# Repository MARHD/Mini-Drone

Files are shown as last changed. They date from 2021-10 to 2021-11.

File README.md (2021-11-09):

# Mini-Drone
Design of a Mini Drone for University of Cape Town EEE4022S final year project.

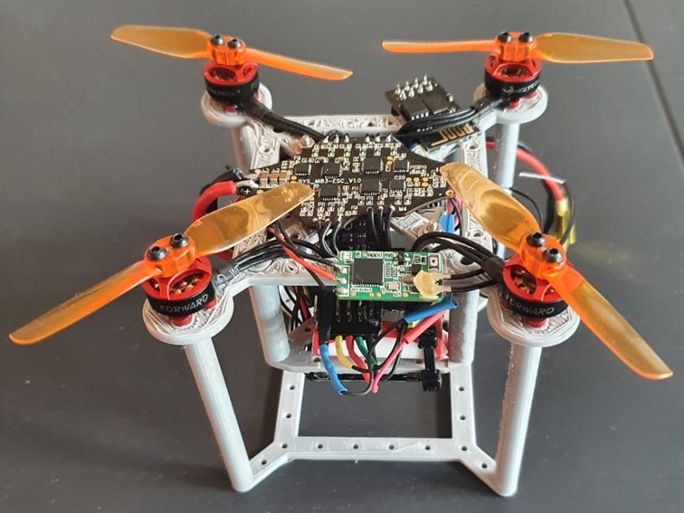
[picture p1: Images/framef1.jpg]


Original project description:
Ardupilot is a professional grade open-source autopilot software stack. This
project requires a student to design a mini-drone (<250g) running the Ardupilot
firmware. An example of analogous drones are linked below. In addition to
designing and building this drone the student must integrate an openflow sensor,
used to facilitate drones holding position by using input from a downwards facing
camera.

Original Deliverables:
1. A literature review briefly summarising drone autopilot software, currently
available mini-drones, recent work using openflow sensors for localisation
2. A functioning mini-drone
3. All design files for (2) including mechanical, electrical, and software build
instructions in a documented public git repository
4. A qualification of the performance of the resulting design
5. The final thesis report, poster, and presentation

## Specifications
- Quadracopter with optical flow sensor and range finder
- Cost: R 5273 (Excluding optical flow sensor, wires, shipping, compatible transmitter and 2S LiPo battery charger), price can be reduced with the replacement of the Pixracer for an Omnibus F4 Pro
- Uses Pixracer R15 flight controller/autopilot, running ArduPilot
- Take-off weight including battery: 107g
- Recommended payload capacity: 60g
- Flight Time with no additional payload: 7-8min hover
- Assembly and test flight time: 2-3hrs (once experienced)

## Getting started
Note: Some assembly tools as well as a means of 3D printing (PLA) are required for assembly.  All 3D printable models are available in [Mechanical Design](./Mechanical%20Design) as Fusion 360 design files, as well as stl files

All required components and suppliers are listed in the following [BOM](./Instructions/BOM.xlsx)

Build instructions are available [here](./Instructions/README.md)

Read through the written report to learn how the components were chosen. Available [here](./report.pdf)

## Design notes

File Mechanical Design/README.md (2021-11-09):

# Design Files

## Final design used. Files to print, [here](./STL%20Files) and file to edit, [here](./Fusion%20Files/Frame%20Final.f3z)



## Older designs
### First design (incomplete). File to edit, [here](./Fusion%20Files/Final%201.f3z)

### Second design (not recommended). File to edit, [here](./Fusion%20Files/Final%202.f3z)

### Third design (works but flimsy upon crash). File to edit, [here](./Fusion%20Files/Final%203.f3z)


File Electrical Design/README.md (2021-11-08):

# Electrical Design

The schematics for the Pixracer flight controller, the microcontroller used on the Pixracer, 
the Flowdeck V2, the Flow Breakout, the Bitcraze Crazyflie 2.1 and the datasheets for,
the PMW3901 (optical flow sensor) and VL53L1X (range finder), are all available here.

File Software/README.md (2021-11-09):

# Software

The compiled .apj file for the project can be found [here](/ArduCopter-4.1%20Custom/Builds/). 
It enables SPI on the port originally designed for the ESP-01 module, and is setup for a pixart 
optical flow sensor (PMW3901)

The ArduCopter parameters used, can be found [here](/ArduCopter-4.%20Custom/Mission%20planner%20Parameters/).
You will still need to calibrate your sensors and some options may need you to follow the ArduCopter guides (such as tuning).

The files which were modified in the firmware can be found [here](/ArduCopter-4.1%20Custom/Modified%20files/).
The unmodified file is also available for comparison.

Finally the Source code for the build of ArduCopter used is available [here](/ArduCopter-4.1%20Custom/Source/)

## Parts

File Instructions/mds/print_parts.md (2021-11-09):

# Printing & assembling plastic parts

1. Print the two .stl files, [here](/./Mechanical%20Design/STL%20Files/Frame_top.stl) for the top frame and [here](/./Mechanical%20Design/STL%20Files/Frame_carriage.stl) for the carriage. Optionally the Stand [here](/./Mechanical%20Design/STL%20Files/Stand.stl) can also be printed.



2. Use a hobby knife to remove the 3D printed supports from these locations. 

 

3. Rotate the carriage such that the foreward arrow is facing foreward, and the posts are facing upwards. 



4. Then rotate the top frame such that the foreward arrow is also facing foreward, and the posts are facing downwards. 



5. Use either a hobby knife or a de-burring tool to clean up any imperfections on the large post holes, the large motor holes on the upper frame and the posts of the carriage. 



6. Apply some super glue into each of the large post holes on the top frame.

  

7. Fit the two parts together with the large holes of the top frame on the carriage posts, such that the top of the posts are flush with the top carriage, as seen in the previous image. 
 
8. Let the glue dry...  

9. Move onto [Mounting the Pixracer](./mount_pixracer.md)

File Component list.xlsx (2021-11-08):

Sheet: Sheet1
Component | Amount | Ind Price | Price | Total | Weight (g) | Link
Motor | 4 | 0 | 0 | 1161.06 | 21.2 | https://hobbyking.com/en_us/brushed-motor-4-pcs-per-set.html?queryID=001191b567772c1bde66302cd4100a57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
Frame | 1 | 0 | 0 |  |  | https://www.rcworld.co.za/product_details.php?proid=298
Mosfets | 4 | 2.3 | 9.2 |  |  | https://flyingrobot.co/collections/speed-controllers/products/flycolor-raptor-bls-pro-blheli_s-30a-2-4s-dshot-brushless-esc
Flight Controller | 1 | 422.5 | 422.5 |  |  | https://www.rcworld.co.za/product_details.php?proid=1357
Battery | 1 | 288.36 | 288.36 |  |  | https://www.rcworld.co.za/product_details.php?proid=308
Receiver | 1 | 280 | 280 |  |  | https://www.goblinhobbies.co.za/fpv/receiver/frsky-xm-sbus-mini-receiver.html
Camera | 1 | 0 | 0 |  | 1.6 | https://store.bitcraze.io/collections/decks/products/flow-deck-v2
 |  |  |  |  |  |  |  |  |  | Choices based on stock availability
for ardupilot
168Mhz and 1MB is minimum on mC
100mm 1s drone | weight | maybe
motors |  | 11 |  | https://micro-motor-warehouse.com/collections/all-motors/products/cl-0716-17 | . |  |  |  |  |  |  | FC requirements
frame | 28 | 10 | 11 | https://www.rcworld.co.za/product_details.php?proid=292 | https://flyingrobot.co/collections/frames-1/products/beta95x-v3-frame-kit | https://www.rcworld.co.za/product_details.php?proid=298 | . |  |  |  |  | Support ardupilot
fc | 5 | 11 | 7 | https://www.rcworld.co.za/product_details.php?proid=1357 | . |  |  |  |  |  |  | 168Mhz and 1MB
receiver | 3 | 1 |  | https://www.rcworld.co.za/product_details.php?proid=1384 | . |  |  |  |  |  |  | aka STM32F4
camera | 2 | 1.6 |  |  | . |  |  |  |  |  |  | 1S battery
battery | 0 | 14 |  | https://www.rcworld.co.za/product_details.php?proid=198 | . |  |  |  |  |  |  | SPI and I2C because flowdeck needs both
props | 5 | 56 | 13 | https://flyingrobot.co/collections/3inch-propellers/products/hq-durable-prop-t65mm-5cw-5ccw-poly-carbonate | . |  |  |  |  |  |  | cheap
wires+misc | 5
total | 48
150mm drone | weight | maybe
motors |  | 20 |  | https://micro-motor-warehouse.com/products/cl-0820-15 | .
frame | 40 | 35 |  | https://www.rcworld.co.za/product_details.php?proid=1174 | . | https://flyingrobot.co/collections/frames-1/products/tbs-source-podracer-5 | .
fc | 5 |  |  |  | .
receiver | 3 |  |  |  | .
camera | 2 |  |  |  | .
battery | 0 |  |  |  | .
props | 10 | 8 |  | https://flyingrobot.co/collections/4inch-propellers/products/hqprop-t4x2x3-2cw-2ccw-poly-carbonate-grey | .
wires+misc | 10
total | 70
200mm drone | weight | maybe
motors |  | 6.1*4 |  |  | .
frame | 47 | 59 |  | https://www.rcworld.co.za/product_details.php?proid=1356 | . | https://flyingrobot.co/collections/frames-1/products/tbs-source-podracer-5 | .
fc | 5 |  |  |  | .
receiver | 3 |  |  |  | .
camera | 2 |  |  |  | .
battery | 0 |  |  |  | .
props | 15 | 14.8 |  | https://flyingrobot.co/collections/6inch-propellers/products/ethix-k2-bubble-gum-2cw-2ccw-poly-carbonate | .
esc |  | 7x4 |  | https://www.rcworld.co.za/product_details.php?proid=1233 | .
wires+misc | 20
total | 92
Quad or Hexa
El cheapo hex | weight | maybe |  | main |  | alt
motors | 17.5 | 30 or 17.5 | 5 or 2.9 |  | .
frame | 32 | 50 | 62 | https://www.banggood.com/Flywoo-Firefly-Hex-Nano-90mm-GOKU-F4-13A-ESC-4S-1_6-Inch-Hexacopter-Micro-FPV-Racing-Drone-BNF-NO-GPS-Version-w-or-5_8G-450mW-VTX-Cad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 | . | https://www.banggood.com/Flywoo-HEXplorer-LR-4-Hexa-copter-HD-or-Analog-Version-3mm-Arm-Thickness-Carbon-Fiber-Frame-Kit-for-FPV-Racing-RC-Drone-p-1805738.htm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 | .
fc | 8 | 11 |  | https://www.banggood.com/Omnibus-F4SD-32K-Betaflight_3_2_0-STM32-F405-Flight-Controller-OSD-5V-3A-BEC-30_5X30_5mm-p-1211677.html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 | https://www.goblinhobbies.co.za/fpv/controller/xrotor-flight-controller-f4-g3-w-osd-for-fpv-racing.html | http://replacementparts-skyrockettoys-com.3dcartstores.com/2018-Fury-Flight-Board-motor-combo_p_158.html | .
receiver | 3 | 10 |  | https://www.rcworld.co.za/product_details.php?proid=1384 | . | https://flyingrobot.co/collections/rx/products/frsky-xm-receiver | . |  |  |  | component choice table
camera | 2 | 1.6 |  |  | . |  |  |  |  |  | add all trials and tribulations into report
battery |  | 15 |  | 450mah 35/50c | .
props | 6 | 10 |  | https://flyingrobot.co/collections/3inch-propellers/products/hq-durable-prop-t65mm-5cw-5ccw-poly-carbonate | .
esc\mosfet board | 2 | 2 |  | https://www.flyingtech.co.uk/electronics/brushed-mosfet-motor-driver-board-pdb-micro-drone | . |  |  | arduino nano 8g
Arduino + transceiver | 11 | 8+3 |  | https://www.robotics.org.za/ESP-01?search=transceiv | .
wires+misc | 5 | 5 |  | https://www.botshop.co.za/product/dc-dc-step-up-converter-3v-to-5v/ | .
total | 86.5 |  |  |  |  |  |  |  |  |  | eportfolio
El cheapo quad | weight | maybe |  | main |  | alt
motors | 12 | 20 or 12 | 6.1*4=24.4 |  | . | https://flyingrobot.co/collections/brushless-motors/products/f1303-kv5000-1pc-set | .
frame | 28 | 10 |  | https://www.rcworld.co.za/product_details.php?proid=292 | https://flyingrobot.co/collections/frames-1/products/beta95x-v3-frame-kit | https://www.rcworld.co.za/product_details.php?proid=298 | .
fc | 8 | 11 |  | https://www.banggood.com/Omnibus-F4SD-32K-Betaflight_3_2_0-STM32-F405-Flight-Controller-OSD-5V-3A-BEC-30_5X30_5mm-p-1211677.html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 | https://www.goblinhobbies.co.za/fpv/controller/xrotor-flight-controller-f4-g3-w-osd-for-fpv-racing.html | http://replacementparts-skyrockettoys-com.3dcartstores.com/2018-Fury-Flight-Board-motor-combo_p_158.html | .
receiver | 3 | 10 |  | https://www.rcworld.co.za/product_details.php?proid=1384 | . | https://flyingrobot.co/collections/rx/products/frsky-xm-receiver | .
camera | 2 | 1.6 |  |  | . |  |  |  | no bueno
battery |  | 15 |  | 450mah 35/50c | .
props | 4 | 6 |  | https://flyingrobot.co/collections/3inch-propellers/products/hq-durable-prop-t65mm-5cw-5ccw-poly-carbonate | .
esc\mosfet board | 2 | 2 | 7x4=28 | https://www.flyingtech.co.uk/electronics/brushed-mosfet-motor-driver-board-pdb-micro-drone | . | https://www.rcworld.co.za/product_details.php?proid=1233 | .
Arduino + transceiver | 11 | 8+3 |  | https://www.robotics.org.za/ESP-01?search=transceiv | .
wires+misc | 5 | 5 |  | https://www.botshop.co.za/product/dc-dc-step-up-converter-3v-to-5v/ | .
total | 75
El cheapo quad brushless | weight | maybe |  | main |  | alt
motors | 28 | 20 or 12 | 6.1*4=24.4 |  | . | https://flyingrobot.co/collections/brushless-motors/products/f1303-kv5000-1pc-set | .
frame | 10 | 10 |  | https://www.rcworld.co.za/product_details.php?proid=292 | https://flyingrobot.co/collections/frames-1/products/beta95x-v3-frame-kit | https://www.rcworld.co.za/product_details.php?proid=298 | .
fc | 8 | 11 |  | https://www.banggood.com/Omnibus-F4SD-32K-Betaflight_3_2_0-STM32-F405-Flight-Controller-OSD-5V-3A-BEC-30_5X30_5mm-p-1211677.html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 | https://www.goblinhobbies.co.za/fpv/controller/xrotor-flight-controller-f4-g3-w-osd-for-fpv-racing.html | http://replacementparts-skyrockettoys-com.3dcartstores.com/2018-Fury-Flight-Board-motor-combo_p_158.html | .
receiver | 3 | 10 |  | https://www.rcworld.co.za/product_details.php?proid=1384 | . | https://flyingrobot.co/collections/rx/products/frsky-xm-receiver | .
camera | 2 | 1.6 |  |  | .
battery |  | 15 |  | 450mah 35/50c | .
props | 4 | 6 |  | https://flyingrobot.co/collections/3inch-propellers/products/hq-durable-prop-t65mm-5cw-5ccw-poly-carbonate | .
esc\mosfet board | 28 | 2 | 7x4=28 | https://www.flyingtech.co.uk/electronics/brushed-mosfet-motor-driver-board-pdb-micro-drone | . | https://www.rcworld.co.za/product_details.php?proid=1233 | .
Arduino + transceiver | 11 | 8+3 |  | https://www.robotics.org.za/ESP-01?search=transceiv | .
wires+misc | 5 | 5 |  | https://www.botshop.co.za/product/dc-dc-step-up-converter-3v-to-5v/ | .
total | 99
Big money hex | weight | maybe | alt | main |  | alt
motors | 17.5 | 30 or 17.5 | 6.1*6 |  | . | https://flyingrobot.co/collections/brushless-motors/products/f1303-kv5000-1pc-set | .
frame | 32 | 50 | 62 | https://www.banggood.com/Flywoo-Firefly-Hex-Nano-90mm-GOKU-F4-13A-ESC-4S-1_6-Inch-Hexacopter-Micro-FPV-Racing-Drone-BNF-NO-GPS-Version-w-or-5_8G-450mW-VTX-Cad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 | . | https://www.banggood.com/Flywoo-HEXplorer-LR-4-Hexa-copter-HD-or-Analog-Version-3mm-Arm-Thickness-Carbon-Fiber-Frame-Kit-for-FPV-Racing-RC-Drone-p-1805738.htm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 | .
fc | 11 | 10.5 |  | https://store.mrobotics.io/mRo-PixRacer-R15-Official-p/m10023a.htm | https://opwiki.readthedocs.io/en/latest/user_manual/revo/revo.html | https://www.banggood.com/de/Radiolink-Mini-PIX-F4-Flight-Controller-MPU6500-w-or-M8N-GPS-UBX-M8030-For-RC-Drone-FPV-Racing-p-1240423.html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 | .
receiver | 3 | 10 |  | https://www.rcworld.co.za/product_details.php?proid=1384 | . | https://flyingrobot.co/collections/rx/products/frsky-xm-receiver | .
camera | 2 | 1.6 |  |  | .
battery |  | 15 |  | 450mah 35/50c | .
props | 6 | 6 | 1*6 | https://flyingrobot.co/collections/3inch-propellers/products/hq-durable-prop-t65mm-5cw-5ccw-poly-carbonate | .
esc\mosfet board | 2 | 7x4=28 | 2 | https://www.flyingtech.co.uk/electronics/brushed-mosfet-motor-driver-board-pdb-micro-drone | .
wires+misc | 8 |  |  | https://www.botshop.co.za/product/dc-dc-step-up-converter-3v-to-5v/ | .
total | 81.5
Big money quad | weight | maybe | alt | main |  | alt
motors | 12 | 20 or 12 | 6.1*4=24.4 |  | . | https://flyingrobot.co/collections/brushless-motors/products/f1303-kv5000-1pc-set | .
frame | 28 | 10 |  | https://www.rcworld.co.za/product_details.php?proid=292 | https://flyingrobot.co/collections/frames-1/products/beta95x-v3-frame-kit | https://www.rcworld.co.za/product_details.php?proid=298 | .
fc | 11 | 10.5 |  | https://store.mrobotics.io/mRo-PixRacer-R15-Official-p/m10023a.htm | https://opwiki.readthedocs.io/en/latest/user_manual/revo/revo.html | https://www.banggood.com/de/Radiolink-Mini-PIX-F4-Flight-Controller-MPU6500-w-or-M8N-GPS-UBX-M8030-For-RC-Drone-FPV-Racing-p-1240423.html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 | .
receiver | 3 | 10 |  | https://www.rcworld.co.za/product_details.php?proid=1384 | . | https://flyingrobot.co/collections/rx/products/frsky-xm-receiver | .
camera | 2 | 1.6 |  |  | .
battery |  | 15 |  | 450mah 35/50c | .
props | 4 | 6 | 1*6 | https://flyingrobot.co/collections/3inch-propellers/products/hq-durable-prop-t65mm-5cw-5ccw-poly-carbonate | .
esc\mosfet board | 2 | 7x4=28 | 2 | https://www.flyingtech.co.uk/electronics/brushed-mosfet-motor-driver-board-pdb-micro-drone | . | https://www.rcworld.co.za/product_details.php?proid=1233 | .
wires+misc | 5 | 5 |  | https://www.botshop.co.za/product/dc-dc-step-up-converter-3v-to-5v/ | .
total | 67
Big money quad brushless | weight | maybe | alt | main |  | alt
motors | 28 | 20 or 12 | 7*4=28 |  | . | https://flyingrobot.co/collections/brushless-motors/products/f1303-kv5000-1pc-set | .
frame | 28 | 10 |  | https://www.rcworld.co.za/product_details.php?proid=292 | https://flyingrobot.co/collections/frames-1/products/beta95x-v3-frame-kit | https://www.rcworld.co.za/product_details.php?proid=298 | .
fc | 11 | 10.5 |  | https://store.mrobotics.io/mRo-PixRacer-R15-Official-p/m10023a.htm | https://opwiki.readthedocs.io/en/latest/user_manual/revo/revo.html | https://www.banggood.com/de/Radiolink-Mini-PIX-F4-Flight-Controller-MPU6500-w-or-M8N-GPS-UBX-M8030-For-RC-Drone-FPV-Racing-p-1240423.html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 | .
receiver | 3 | 10 |  | https://www.rcworld.co.za/product_details.php?proid=1384 | . | https://flyingrobot.co/collections/rx/products/frsky-xm-receiver | .
camera | 2 | 1.6 |  |  | .
battery |  | 15 |  | 450mah 35/50c | .
props | 4 | 6 | 1*6 | https://flyingrobot.co/collections/3inch-propellers/products/hq-durable-prop-t65mm-5cw-5ccw-poly-carbonate | .
esc\mosfet board | 28 | 7x4=28 | 2 | https://www.flyingtech.co.uk/electronics/brushed-mosfet-motor-driver-board-pdb-micro-drone | . | https://www.rcworld.co.za/product_details.php?proid=1233 | .
wires+misc | 5 | 5 |  | https://www.botshop.co.za/product/dc-dc-step-up-converter-3v-to-5v/ | .
total | 109

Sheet: Sheet2
Quad or Hexa
El Cheapo Hex | Weight | Price | Complexity | Link |  | Performance
Motors | 17.5 |  |  | Motor (https://micro-motor-warehouse.com/collections/all-motors/products/cl-0716-17) |  | Hover Throttle | All-up Weight | Efficiency@Max | Hover time | Bat Load | Thrust-Weight | Specific Thrust
Frame | 15 | 105 |  | Rod (http://cmchobbies.co.za/shop/carbon-fibre-Build-materials/carbon-solid-rod-5mm) |  | 76% | 84g | 30% | 3.3min | 25C | 1.3:1 | 3.48 g/W
FC | 8 | 500 |  | FC (https://www.banggood.com/Omnibus-F4SD-32K-Betaflight_3_2_0-STM32-F405-Flight-Controller-OSD-5V-3A-BEC-30_5X30_5mm-p-1211677.html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)
Receiver | 3 | 300 |  | Rec (https://flyingrobot.co/collections/rx/products/frsky-xm-receiver)
Flow Deck | 2 |  |  | Flow (https://www.bitcraze.io/products/flow-deck-v2/)
Battery |  | 173 |  | Bat (https://flyingrobot.co/collections/1s/products/f949-battery-1s-500mah)
Props | 6 | 110 |  | Prop (https://flyingrobot.co/collections/3inch-propellers/products/hq-durable-prop-t65mm-5cw-5ccw-poly-carbonate)
ESC\Mosfet Board | 2 | 180 |  | Mos (https://www.flyingtech.co.uk/electronics/brushed-mosfet-motor-driver-board-pdb-micro-drone)
Arduino + Transceiver | 11 | 45 |  | Telem (https://www.robotics.org.za/ESP-01?search=transceiv)
Wires + Misc | 5 | 31 |  | 5V (https://www.botshop.co.za/product/dc-dc-step-up-converter-3v-to-5v/)
Total | 69.5 | 1444 | 45/50
Including Battery | 83.5
El Cheapo Quad | Weight | Price | Complexity | Link |  | doesn’t fly
Motors | 12 |  |  | Motor (https://micro-motor-warehouse.com/collections/all-motors/products/cl-0716-17)
Frame | 10 | 105 |  | Rod (http://cmchobbies.co.za/shop/carbon-fibre-Build-materials/carbon-solid-rod-5mm)
FC | 8 | 500 |  | FC (https://www.banggood.com/Omnibus-F4SD-32K-Betaflight_3_2_0-STM32-F405-Flight-Controller-OSD-5V-3A-BEC-30_5X30_5mm-p-1211677.html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)
Receiver | 3 | 300 |  | Rec (https://flyingrobot.co/collections/rx/products/frsky-xm-receiver)
Flow Deck | 2 |  |  | Flow (https://www.bitcraze.io/products/flow-deck-v2/)
Battery |  | 173 |  | Bat (https://flyingrobot.co/collections/1s/products/f949-battery-1s-500mah)
Props | 4 | 55 |  | Prop (https://flyingrobot.co/collections/3inch-propellers/products/hq-durable-prop-t65mm-5cw-5ccw-poly-carbonate)
ESC\Mosfet Board | 2 | 180 |  | Mos (https://www.flyingtech.co.uk/electronics/brushed-mosfet-motor-driver-board-pdb-micro-drone)
Arduino + Transceiver | 11 | 45 |  | Telem (https://www.robotics.org.za/ESP-01?search=transceiv)
Wires + Misc | 5 | 31 |  | 5V (https://www.botshop.co.za/product/dc-dc-step-up-converter-3v-to-5v/)
Total | 57 | 1389 | 42/50
Including Battery | 71
El Cheapo Quad Brushless | Weight | Price | Complexity | Link |  | Performance
Motors | 28 | 840 |  | Motor (https://flyingrobot.co/collections/brushless-motors/products/f10-7500kv-1pc-set) |  | Hover Throttle | All-up Weight | Efficiency@Max | Hover time | Bat Load | Thrust-Weight | Specific Thrust
Frame | 10 | 105 |  | Rod (http://cmchobbies.co.za/shop/carbon-fibre-Build-materials/carbon-solid-rod-5mm) |  | 45% | 125g | 53.5% | 6.1min | 42.3C | 2.6:1 | 4.57 g/W
FC | 8 | 500 |  | FC (https://www.banggood.com/Omnibus-F4SD-32K-Betaflight_3_2_0-STM32-F405-Flight-Controller-OSD-5V-3A-BEC-30_5X30_5mm-p-1211677.html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)
Receiver | 3 | 300 |  | Rec (https://flyingrobot.co/collections/rx/products/frsky-xm-receiver)
Flow Deck | 2 |  |  | Flow (https://www.bitcraze.io/products/flow-deck-v2/)
Battery |  | 235 |  | Bat (https://flyingrobot.co/collections/1s/products/f949-battery-1s-500mah)
Props | 4 | 55 |  | Prop (https://flyingrobot.co/collections/3inch-propellers/products/hq-durable-prop-t65mm-5cw-5ccw-poly-carbonate)
ESC\Mosfet Board | 24 | 360 |  | ESC (https://www.goblinhobbies.co.za/fpv/esc/racerstar-rs20a-v2-new-20a-blheli-s-opto-2-4s-esc-support-oneshot42-multishot-16-5-dshot600.html)
Arduino + Transceiver | 11 | 45 |  | Telem (https://www.robotics.org.za/ESP-01?search=transceiv)
Wires + Misc | 5
Total | 95 | 2440 | 40/50
Including Battery | 125
Big Money Hex | Weight | Price | Complexity | Link |  | Performance
Motors | 17.5 |  |  | Motor (https://micro-motor-warehouse.com/collections/all-motors/products/cl-0716-17) |  | Hover Throttle | All-up Weight | Efficiency@Max | Hover time | Bat Load | Thrust-Weight | Specific Thrust
Frame | 15 | 105 |  | Rod (http://cmchobbies.co.za/shop/carbon-fibre-Build-materials/carbon-solid-rod-5mm) |  | 70% | 76g | 30% | 4min | 25C | 1.5:1 | 3.76 g/W
FC | 11 | 2700 |  | FC (https://store.mrobotics.io/mRo-PixRacer-R15-Official-p/m10023a.htm)
Receiver | 3 | 300 |  | Rec (https://flyingrobot.co/collections/rx/products/frsky-xm-receiver)
Flow Deck | 2 |  |  | Flow (https://www.bitcraze.io/products/flow-deck-v2/)
Battery |  | 173 |  | Bat (https://flyingrobot.co/collections/1s/products/f949-battery-1s-500mah)
Props | 6 | 110 |  | Prop (https://flyingrobot.co/collections/3inch-propellers/products/hq-durable-prop-t65mm-5cw-5ccw-poly-carbonate)
ESC\Mosfet Board | 2 | 180 |  | Mos (https://www.flyingtech.co.uk/electronics/brushed-mosfet-motor-driver-board-pdb-micro-drone)
Wires + Misc | 5 | 31 |  | 5V (https://www.botshop.co.za/product/dc-dc-step-up-converter-3v-to-5v/)
Total | 61.5 | 3599 | 35/50
Including Battery | 75.5
Big Money Quad | Weight | Price | Complexity | Link |  | Performance
Motors | 12 |  |  | Motor (https://micro-motor-warehouse.com/collections/all-motors/products/cl-0716-17) |  | Hover Throttle | All-up Weight | Efficiency@Max | Hover time | Bat Load | Thrust-Weight | Specific Thrust
Frame | 10 | 105 |  | Rod (http://cmchobbies.co.za/shop/carbon-fibre-Build-materials/carbon-solid-rod-5mm) |  | 84% | 63g | 30.6% | 4min | 17C | 1.2:1 | 3.15 g/W
FC | 11 | 2700 |  | FC (https://store.mrobotics.io/mRo-PixRacer-R15-Official-p/m10023a.htm)
Receiver | 3 | 300 |  | Rec (https://flyingrobot.co/collections/rx/products/frsky-xm-receiver)
Flow Deck | 2 |  |  | Flow (https://www.bitcraze.io/products/flow-deck-v2/)
Battery |  | 173 |  | Bat (https://flyingrobot.co/collections/1s/products/f949-battery-1s-500mah)
Props | 4 | 55 |  | Prop (https://flyingrobot.co/collections/3inch-propellers/products/hq-durable-prop-t65mm-5cw-5ccw-poly-carbonate)
ESC\Mosfet Board | 2 | 180 |  | Mos (https://www.flyingtech.co.uk/electronics/brushed-mosfet-motor-driver-board-pdb-micro-drone)
Wires + Misc | 5 | 31 |  | 5V (https://www.botshop.co.za/product/dc-dc-step-up-converter-3v-to-5v/)
Total | 49 | 3544 | 33/50
Including Battery | 63
Big Money Quad Brushless | Weight | Price | Complexity | Link |  | Performance
Motors | 28 | 840 |  | Motor (https://flyingrobot.co/collections/brushless-motors/products/f10-7500kv-1pc-set) |  | Hover Throttle | All-up Weight | Efficiency@Max | Hover time | Bat Load | Thrust-Weight | Specific Thrust
Frame | 10 | 105 |  | Rod (http://cmchobbies.co.za/shop/carbon-fibre-Build-materials/carbon-solid-rod-5mm) |  | 43% | 117g | 53.5% | 6.7min | 42.3C | 2.8:1 | 4.67 g/W
FC | 11 | 2700 |  | FC (https://store.mrobotics.io/mRo-PixRacer-R15-Official-p/m10023a.htm)
Receiver | 3 | 300 |  | Rec (https://flyingrobot.co/collections/rx/products/frsky-xm-receiver)
Flow Deck | 2 |  |  | Flow (https://www.bitcraze.io/products/flow-deck-v2/)
Battery |  | 235 |  | Bat (https://flyingrobot.co/collections/1s/products/f949-battery-1s-500mah)
Props | 4 | 55 |  | Prop (https://flyingrobot.co/collections/3inch-propellers/products/hq-durable-prop-t65mm-5cw-5ccw-poly-carbonate)
ESC\Mosfet Board | 24 | 360 |  | ESC (https://www.goblinhobbies.co.za/fpv/esc/racerstar-rs20a-v2-new-20a-blheli-s-opto-2-4s-esc-support-oneshot42-multishot-16-5-dshot600.html)
Wires + Misc | 5
Total | 87 | 4595 | 31/50
Including Battery | 117
System | Price | Weight excl battery | Flight time | Throttle | Complexity | Recommend?
System 1 - Cheaper hex, brushed | 1444 | 69.5 | 3.3min | 76% | 45/50 | No
System 2 - Cheaper Quad, brushed | 1389 | 57 | 0 | 0 | 42/50 | No
System 3 - Cheaper Quad, brushless | 2440 | 95 | 6.1min | 45% | 40/50 | Yes
System 4 - Expensive hex, brushed | 3599 | 61.5 | 4min | 70% | 35/50 | Maybe, with tweaks
System 5 - Expensive quad, brushed | 3544 | 49 | 4min | 84% | 33/50 | No
System 6 - Expensive quad, brushless | 4595 | 87 | 6.7min | 43% | 31/50 | Yes
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

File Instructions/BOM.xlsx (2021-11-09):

Components | Weight | Price alltogether | Qty | Link
Motors | 16 | R 800 | 4 | HGLRC 1103 8000KV (https://boyztoyz.co.za/product/hglrc-fd1103-8000kv-brushless-motor/)
Frame | 15 |  | 1 | 3D printed
FC | 11 | R 2700 | 1 | Pixracer (https://store.mrobotics.io/mRo-PixRacer-R15-Official-p/m10023a.htm)
Receiver | 3 | R 300 | 1 | XM+ (https://flyingrobot.co/collections/rx/products/frsky-xm-receiver)
Flow Deck | 2 |  | 1 | Flow Deck V2 (https://www.bitcraze.io/products/flow-deck-v2/)
Battery | 30 | R 236 | 1 | Onbo 460mAh 75C 2S (https://www.rclipo.co.za/lipo/2-cell/onbo-460mah-2s-75c-lipo-detail)
Props | 4 | R 55 | 1 | 65mm HQ Prop (https://flyingrobot.co/collections/3inch-propellers/products/hq-durable-prop-t65mm-5cw-5ccw-poly-carbonate)
ESC | 6 | R 570 | 1 | DYS ELF 10A ESC (https://flyingrobot.co/collections/4in1-escs/products/dys-elf-4in1-10a-esc) | Better replacement (https://boyztoyz.co.za/product/hglrc-fd13a-bl_s-3-6s-13a-4in1-esc-16-x-16/)
BEC + V,C sense | 15 | R 550 | 1 | PBM (https://flyingrobot.co/products/power-brick-mini)
conn1 |  |  | 4 | JST GH 6-pin male (https://za.rs-online.com/web/p/wire-housings-plugs/7521743/) | need pins as well
conn2 |  |  | 1 | JST GH 5-pin male (https://za.rs-online.com/web/p/wire-housings-plugs/7521740/) | need pins as well
conn3 |  |  | 1 | Dupont 1x1 female (https://www.netram.co.za/connectors/9038-1-way-dupont-female-connector-pack-of-10.html)
conn4 |  |  | 3 | Dupont 1x4 female (https://www.netram.co.za/connectors/9035-4-way-dupont-female-connector-pack-of-10.html)
conn5 |  |  | 2 | 4x1 male breakaway (https://www.netram.co.za/headers/9447-header-male-40x2-breakaway.html) | or 4x2 male header
Wires + Misc | 5
Total | 107 | R 5211

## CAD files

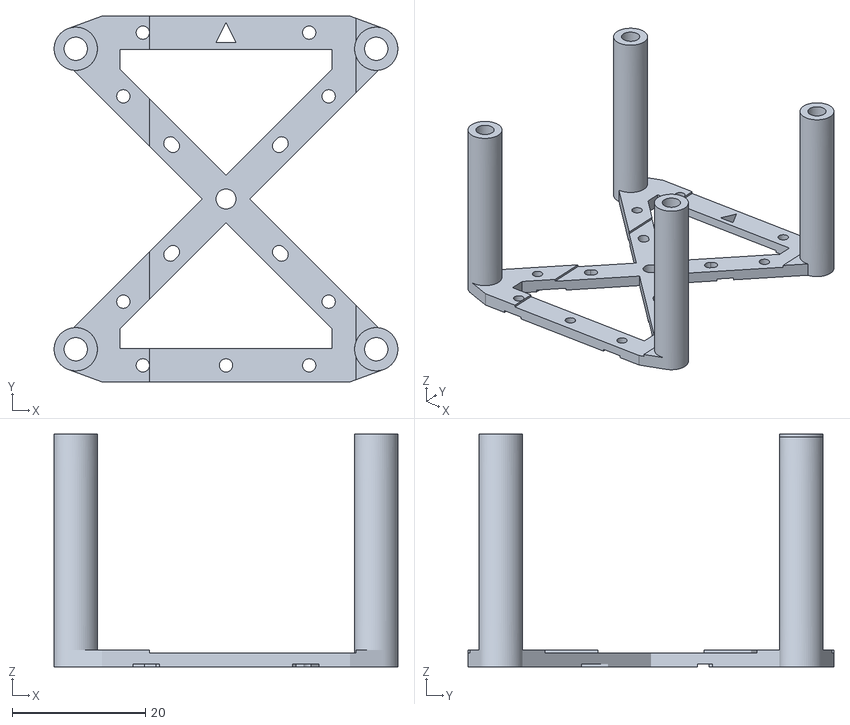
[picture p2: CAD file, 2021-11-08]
Mechanical Design/STL Files/Frame_carriage.stl
51.7 x 55.0 x 35.0

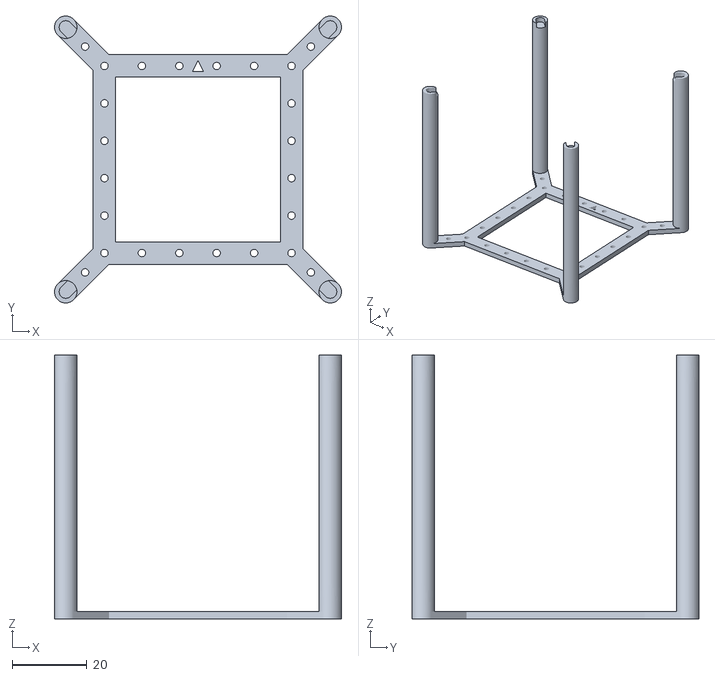
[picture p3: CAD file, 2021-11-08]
Mechanical Design/STL Files/Stand.stl
76.7 x 76.7 x 70.6

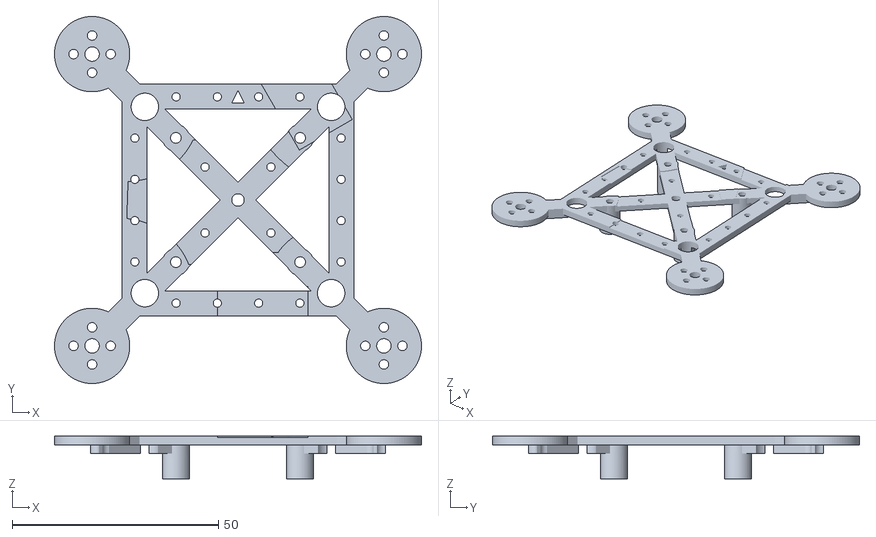
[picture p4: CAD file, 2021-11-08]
Mechanical Design/STL Files/Frame_top.stl
88.9 x 88.9 x 10.4

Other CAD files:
Mechanical Design/Components/65mm Press-Fit Prop v1.f3d
Mechanical Design/Components/ESP-01S (ESP8266) Board Module v1.f3d
Mechanical Design/Components/Motor - LDARC 1103-7800 v2.f3z
Mechanical Design/Components/Pixracer Flight Controller v1.f3d
Mechanical Design/Fusion Files/Frame 1.f3z

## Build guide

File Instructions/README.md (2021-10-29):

Build Instructions
==
## Required tools
* Access to a 3D printer capable of printing PLA or ABS
* 2mm flathead screwdriver (or whichever is needed for the M2 screws you bought)
* M2 socket or wrench (or even a pair of pliers)
* 1.5mm Torx screwdriver (for 1103 motors included screws)
* Wire Cutters
* Wire Strippers
* Soldering Iron
* Solder (preferably leaded with flux)

## Notes on assembly
* Note1: Loctite should be used on screws only once confident everything is correctly assembled. Or locknuts could be used instead. 

* Note2: Once all parts have been gathered and printed, the drone can be assembled within around 3-4 hours. This excludes flight testing and debugging, so first time assembly will take longer.

## Order of Assembley:

1. [Order Components](BOM.xlsx)
1. [Print & assemble Parts](mds/print_parts.md)
1. [Mount Pixracer](mds/mount_pixracer.md)
1. [Wire & Mount Flowdeck sensor board](mds/mount_flow.md)
1. [Replace XT60 & battery connector with XT30](mds/xt30.md)
1. [Wire & Mount Power Brick](mds/power_brick.md)
1. [Wire & Mount motors + ESC](mds/esc.md)
1. [Wire & Mount receiver](mds/rec.md)
1. [Wire & Mount telemetry](mds/telem.md)
1. [Mount battery](mds/mount_bat.md)
1. [Installing firmware](mds/ardu.md)
1. [Configuring ArduPilot](mds/config.md)
1. [Installing Propellers](mds/props.md)
1. [Tuning](mds/tune.md)

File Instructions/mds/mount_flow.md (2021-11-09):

# Wiring and Mounting the Flowdeck V2

Skip this step if you do not have a flowdeck or optical flow sensor/rangefinder

1. Find one of your JST GH 6-pin cables as well as a breakaway male header (break 2, 4 way pins and glue together) with 6 assorted wires.

Then Cut the 6-pin JST GH cable to be approximately 14 cm and remove the insulation from the newly cut end.



2. Solder 3 of the the wires to the Flowdeck V2 (from the 6-pin JST cable), matching the connections to the two images below. 

Alternatively a header for the Flowdeck could be purchased and the wires soldered to that instead.

The other wires can either be removed from the connector or heat shrink placed over the ends to prevent shorting.

  

3. Next solder 6 wires onto the dupont header according to the diagram below, and heat shrink over the wires once done.

 

4. Cut the other end of the 6 wires to approximately 8 cm, remove the insulation and solder onto the flowdeck according to the diagram below.

NB: Also use another short wire to connect the two power pins as shown by the thicker red wire in image 2.

NB2: The red 3.3V wire connect to the flowdeck and to the telemetry module (so an additional wire should be soldered). 

 

5. Plug the newly created cables into the ports on the Pixracer, to ensure wire lengths are correct. 

 

6. Rotate the frame to be upside down and place clear glue onto the 4 pads indicated below.



7. Place the Flowdeck onto the 4 pads, with the arrow facing towards the foreward arrow of the frame and keeping the edge of the flowdeck inline with the edge of the frame carriage.

Hold the Flowdeck in place until it wont slide around anymore. Then let the glue dry...



8. Move onto [Replacing the XT60 connectors](./xt30.md)

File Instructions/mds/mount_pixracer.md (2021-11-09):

# Mounting the Pixracer

1. Find the arrow indicating foreward on the Pixracer.



2. Rotate the Pixracer 180 degrees, keeping the arrow facing forewards and fit the Pixracer into the frame as seen in the image, with the foreward arrow aligned with the arrow on the frame. 

It might need to be put in at an angle, but should clip into the frame when correctly located.



4. Place at least two M2 screws into the mounting holes, with the nuts on the otherside and tighten with a screw driver, while holding the nut steady with either a socket or pliers.



6. Move onto [Wiring and mounting the Flowdeck V2](./mount_flow.md)

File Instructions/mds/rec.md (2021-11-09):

# Wiring and Mounting the receiver

1. Find your 5 pin JST GH cable, cut one end off and strip the insulation back slightly. Then solder the uninsulated ends onto the receiver according to the following diagrams.

 

3. Either apply some thick double sided tape to the area on the top frame, or some clear glue.



4. Place the receiver onto the tape or glue and let it settle.



5. Plug the 5 pin JST cable into the RC port of the Pixracer.



6. Heat shrink the end of the receivers antennas together and route it out of the way down the side of the drone to the bottom. 

 

7. Move onto [Wiring and Mounting the telemetry module](./telem.md)

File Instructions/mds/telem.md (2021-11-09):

# Wiring and Mounting the Telemetry module

1. Get 5 dupont female wires or a 4x2 dupont female connector and cut the other end of the wires to around 14-15 cm.

Also find another 6 pin JST GH cable and cut one end, removing the insulation from both wires.

 
 
2. Use heat shrink and solder the cables together according to the following diagrams.

NB: the 3.3V wire comes from the SPI header we made before, which also connects to the flowdeck. This 3.3V wire is connected to two places on the telemetry module.

 

3. Place clear glue onto the area on the top top frame and place the telemetry module on the glue holding until dry.

 

4. Plug the 6 pin JST cable into the telemetry 1 port of the Pixracer.



5. Move onto [Mounting the battery](./mount_bat.md)

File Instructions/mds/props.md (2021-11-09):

# Installing propellers

1. Find your propellers and place them all with the writing facing upwards so that it is legible.



2. Locate 2 propellers which have "T65" written on them and 2 which have "T65R". 

Or if there is no direction indication, find 2 of each type of prop, with the writing facing upwards or the moulding marks facing downwards, the propeller types should look opposite to each other.

Watch this [video](https://www.youtube.com/watch?v=nc1QG_Njo7Y&t=238s&ab_channel=JoshuaBardwell) to learn how to tell which propeller is for CW or CCW.

 

3. Hold the motors still and fit the propellers onto the motor shafts according to the following diagram, where the "T65" propellers are for CCW rotation and the "T65R" are for CW rotation.

Twisting the propellers will help to get them on. 

NB: Do not push the propellers so far that the shaft is visible above the hole of the propeller.



4. Rotate the propellers on the motor shaft such that the holes line up with the holes in the motor.

Then use the provided motor screws (longer ones) to slowly screw the propeller in place until the motor shaft is just barely flush with the top of the propeller.

 

5. Move onto [Tuning](./tune.md)

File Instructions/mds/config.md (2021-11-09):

# Configuring ArduPilot

1. Download the latest "main" parameter file [here](/./Software/ArduCopter-4.1%20Custom/Mission%20Planner%20Parameters/)

2. With the drone connected via USB, click the "config" button at the top of Mission Planner, followed by the "full parameter list" tab.

 

3. Click on the "Load from file" button on the right hand side and navigate to where you saved the parameter file earlier.

Choose the file and click open.

The parameter list should be updated

 

4. Click on the "Write Params" button on the right, to save these parameters ontp the drone.

Once completed, restart the drone by unplugging and plugging the USB back in.



5. Click on the "Setup button" again, at the top of Mission Planner. Then click on the "Mandatory Hardware" tab. 

Go through each of the sub categories of "Mandatory Hardware" to calibrate the Accelerometers, Gyroscope and compass as well as setting up the transmitter, according to the [ardupilot setup page](https://ardupilot.org/copter/docs/configuring-hardware.html)



6. Move onto [Installing propellers](./props.md)

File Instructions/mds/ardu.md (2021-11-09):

# Installing ArduPilot

Your Pixracer should come with Ardupilot pre-installed. If not, follow the guide [here](https://ardupilot.org/copter/docs/initial-setup.html) to install it

1. Download the latest pre-compiled ArduPilot version [here](/./Software/ArduCopter-4.1%20Custom/Builds/)

2. Install Mission Planner with default settings.



3. Plug your Micro USB cable into the Pixracer and the other end into your computer. 

Then click the connect to COM button on the top right of Mission Planner

 

4. Click on the Setup button at the top of Mission Planner. 

Then click on the Install Firmware button, followed by the Load custom firmware button.

 
 


5. Navigate to where you downloaded the ArduPilot firmware before, choose the file and click open.

The firmware should install after a few minutes.



6. Once installed, restart the Pixracer by simply un-plugging and plugging the USB back in.

7. Move onto [Configuring the firmware](./config.md)

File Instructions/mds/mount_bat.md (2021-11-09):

# Mounting the Battery

1. Place a thin layer of clear tape onto the surface of the battery to prevent the clear glue from bonding to the batteries plastic.

Place clear glue on the areas shown in the carriage of the frame.



3. Slide the battery in, with the power cable nearest to the XT30 connector of the power module.

Hold the battery in place, trying to keep it centered in the carriage long ways and to the side of the SPI connector sticking out of the Pixracer.



4. Let the glue dry...

5. Move onto [Installing the firmware](./ardu.md)

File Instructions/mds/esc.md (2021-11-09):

# Wiring and Mounting the motors and ESC

1. Place the ESC on a flat surface or in helping hands in this orientation.



2. Solder 5 small wires either onto a connector which fits on the ESC signal header, or directly onto the pads (as I have). Then solder the other end of the wires to a 4 way dupont female header and an additional dupont female connector for the GND pin.

The wires should follow the connection diagrams below.

NB: These connectors are tiny so be careful when soldering and moving it around (I would actually recommend a different ESC due to the small connections on this one, mentioned in the BOM file)

 

3. Cut the connectors off of the motor cables and remove a small amount of insulation, then straighten the motor wires so that they aren't crossed.

Flip the ESC over and solder the individual 3 wires of each motor onto the soldering pads of the ESC, keeping the motor wires completely straight.



4. Place padded double sided tape and clear glue in the following pattern on the top frame. 



5. Place the ESC onto the top of the frame as shown. keeping the edge with power wires flush with the frame and the ESC close but not touching the top left screw holding the Pixracer in. Hold the ESC in place until it wont move and let the glue dry...



6. Next place the wires of one motor at the top of the ESC, over the one beside it and the same for the bottom of the ESC, as seen below. i.e. cross the motors.



7. Ensure the middle holes of the motor mounts on the top frame have been deburred as described in: [Printing and Assembling plastic parts](./print_parts.md)



8. Screw the motors in with the provided torx screws(shorter ones), keeping the wires aiming toward the center of the frame. Propellers shouldn't be attached (image was taken after the fact).



9. Tuck the excess motor wires into the cut out areas of the top frame.



10. Connect the signal wires to the large signal header on the Pixracer according to the images in step 2, with the GND wire 2 places below the signal wires.

In this image the black wire is for motor 1, green motor 2..., blue is for GND



11. Move onto [Wiring and Mounting the receiver](./rec.md)

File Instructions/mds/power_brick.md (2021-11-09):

# Wiring and mounting the Power brick

1. Plug the 6 pin JST GH connector into the power brick and into the Pixracer as shown.

 

2. Place the frame upside down and place clear glue onto the center pad of the frame as shown. 



4. Place the Brick onto the glue in the orientation shown below and hold. Hold the brick onto the glue until it doesn't move when you let go. Then let the glue dry...

NB: Snip the long metal pins of the brick should they protrude too much.



6. Move onto [Wiring and mounting the motors + ESC](./esc.md)

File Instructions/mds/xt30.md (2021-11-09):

# Replacing XT60 and battery connector with XT30

Skip to mounting the power brick should you wish to use XT60 connectors instead (battery connector replacement can follow the guide below)

1. Remove the plastic heat shrink from the power brick.

Note the positive and negative symbols on the connector, as well as which side of the Power brick has a male connector vs female.



2. Place the Power brick into helping hands such that the connector you are removing first is aimed directly down. Then turn on your soldering iron and tin the tip with solder.

Heat the large pads of the Power brick XT60 connector and apply leaded solder with flux (The large ground planes might need a strong soldering iron to melt)

3. Once the solder has started to melt on the connector, switch back and forth between heating the two pads, so that they both are being heated simultaneously.

Alternatively using two soldering irons on each of the pads would be easier. 

Keep doing this ensuring you dont hit any other components on the brick. The connector should fall off with gravity, but if not some tweezers can be used for persuasion. However do not pull on the connector if the solder is not melted, or you might rip pads. 

Proceed with the other connector as well...



6. Once both XT60's have been removed. Solder some thicker 14 AWG wire to all 4 of the pads, using colours to distinguish the positive and negative pads.

7. Now cut the wires on the side of the brick which had a female XT60, to be a fairly short 1.8-2 cm and solder a female XT30 onto the ends after removing insulation (dont forget the heat shrink)



8. Cut the remaining wires to be approximately 12 cm. Either solder the other wires directly to the ESC (as I have) or use another XT30 connector if you wish.



9. !Please be careful on this step! 

Cut the wires on the battery one at a time, fitting the heat shrink and soldering to the male XT30 connector.

I.e. Cut one wire, fit heat shrink, solder to XT30 and melt heat shrink on, then continue to the next wire.

NB: If you cut both wires at the same time, the battery will short and spark, worst case it could explode or cause a fire.

 

10. Move onto [Wiring and mounting the power brick](./power_brick.md)

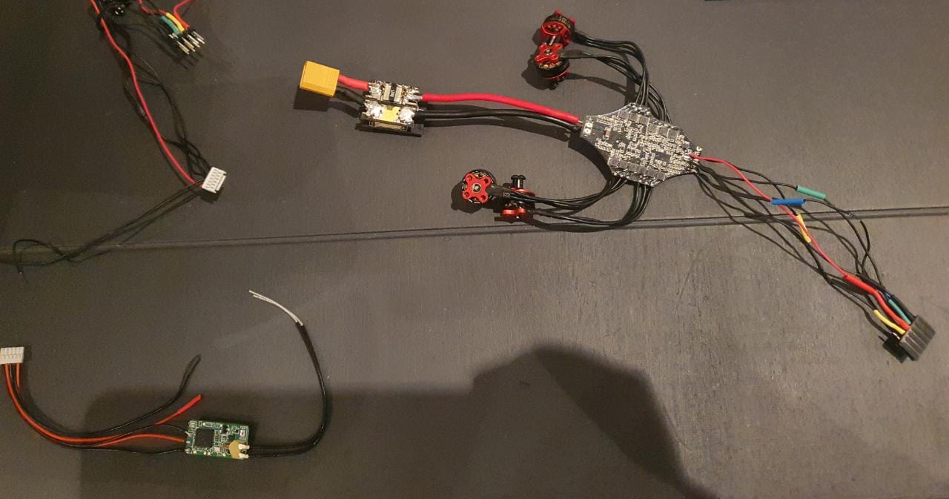
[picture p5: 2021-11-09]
Images/Instructions/allesc3.jpeg

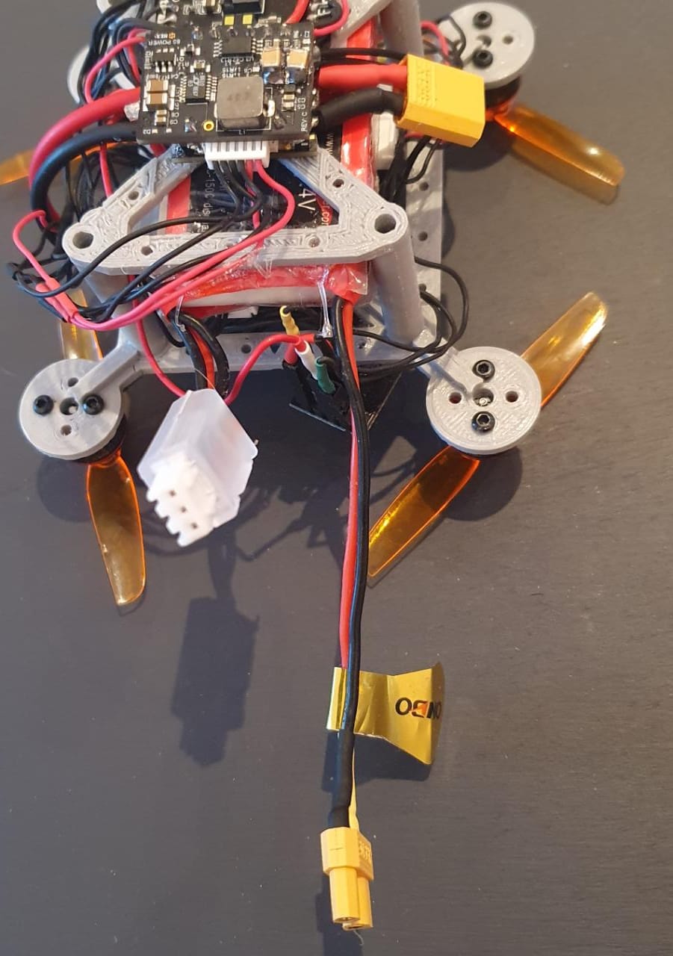
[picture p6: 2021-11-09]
Images/Instructions/batwire2.jpeg

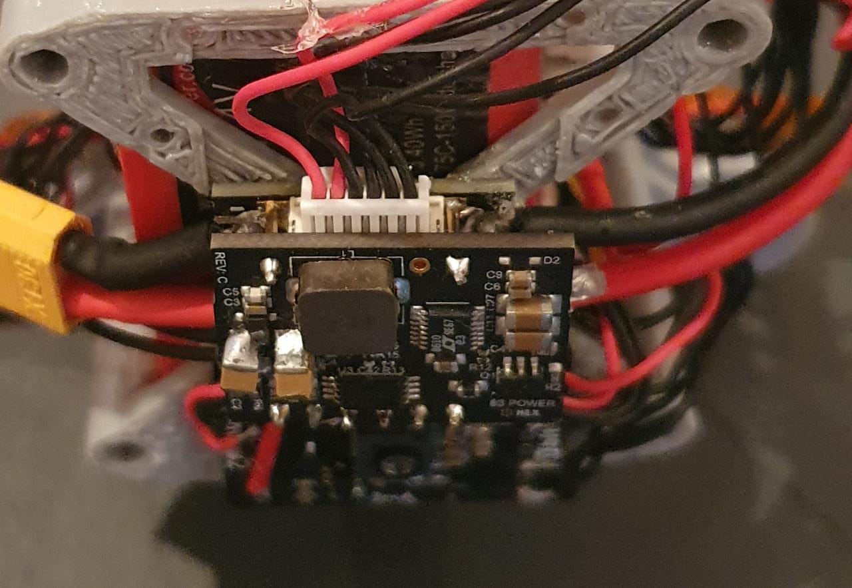
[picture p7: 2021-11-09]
Images/Instructions/brickpwr2.jpeg

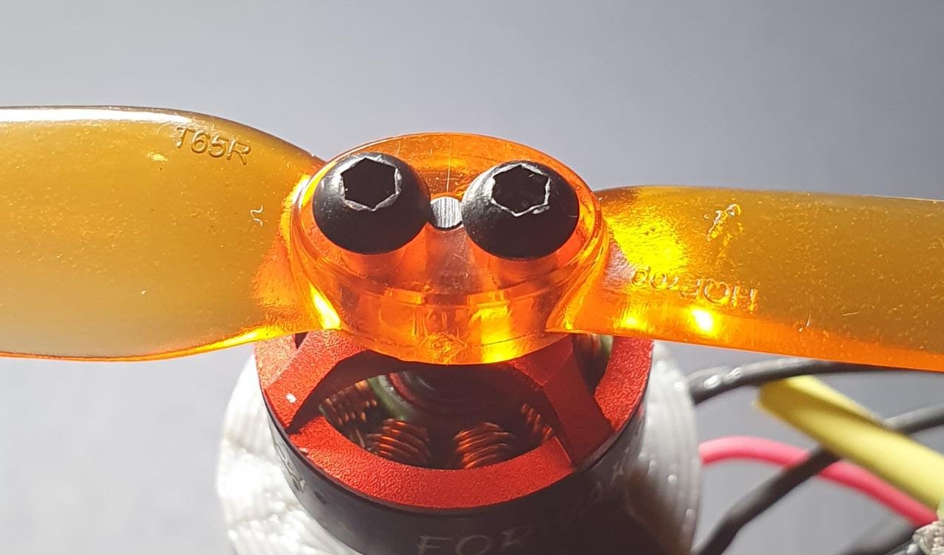
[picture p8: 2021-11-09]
Images/Instructions/screw.jpeg

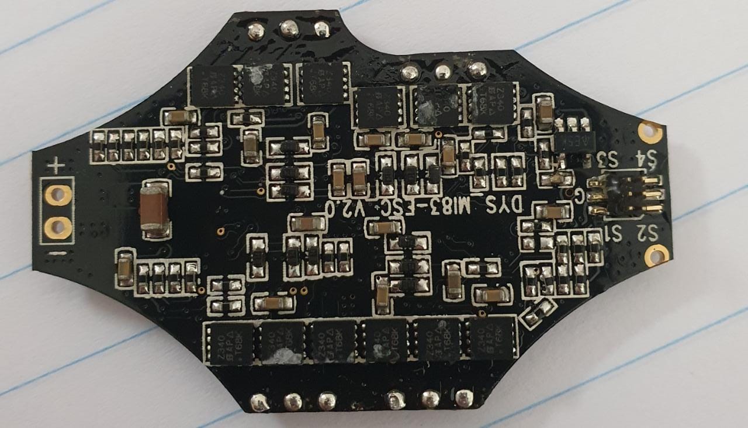
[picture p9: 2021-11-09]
Images/Instructions/esc1.jpeg

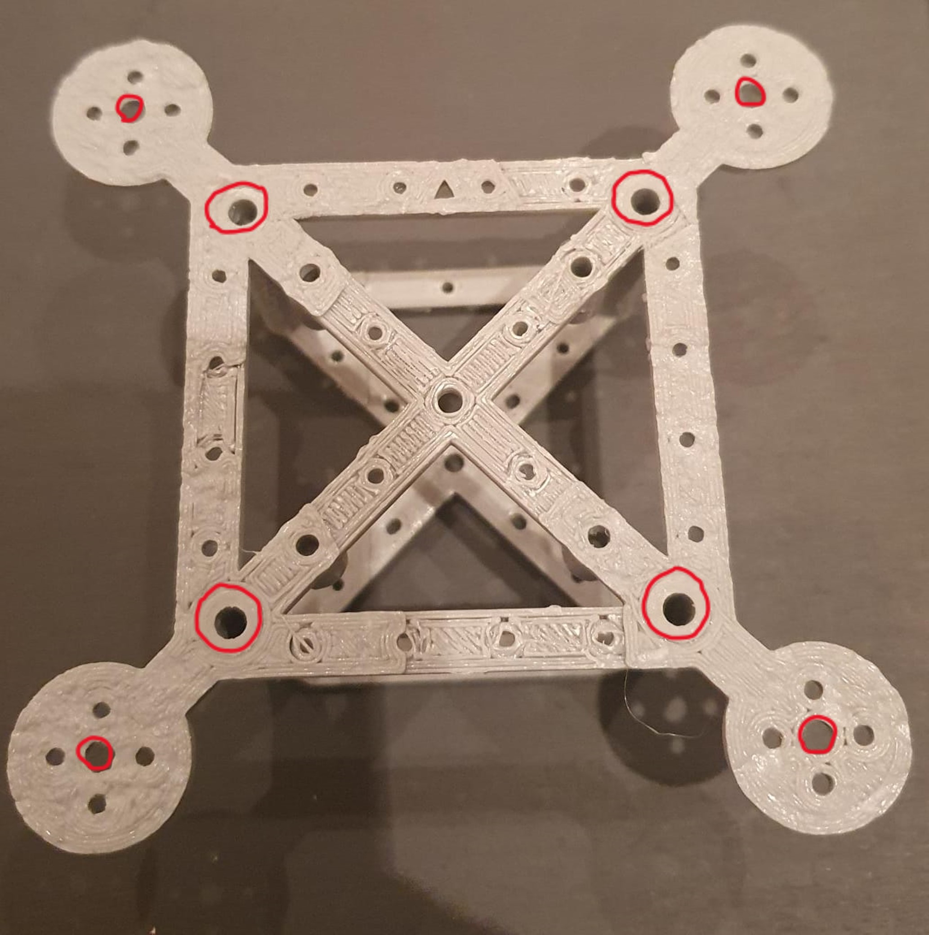
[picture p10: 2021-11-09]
Images/Instructions/bur.jpg

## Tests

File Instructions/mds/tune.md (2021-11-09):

# Tuning the drone

1. Connect the drone to your laptop via USB, then open your computers wifi networks and connect to ArduPilot or PixRacer with the password "ardupilot" or "pixracer" respectively.



2. Next in Mission Planner change the connection type from COM to UDP and click connect. Click ok for the default port number.

You should now be connected via the Wifi telemetry to Mission Planner (powered via USB)

 

3. To fly the drone, I would first plug in via USB, connect to the wifi and mission planner, then plug in the battery, unplug the usb cable and turn on the transmitter. This is to save battery life, as connecting is not always quick.

4. Follow the instructions on the ArduPilot tuning [page](https://ardupilot.org/copter/docs/tuning-process-instructions.html) to get you through your first flight and rough tune (skip to "Pilot’s preparation for first flight" on the page).

Although with the paramter file having being uploaded, the drone should have enough of a tune to be able to at least hover in stabilize mode.



5. Once comfortable flying the drone, move to a large open space or outside on a still day and proceed to following the instructions for AutoTuning the drone, [here](https://ardupilot.org/copter/docs/autotune.html)



6. After doing an autotune proceed to tune the optical flow sensor according to ArduPilots [page](https://ardupilot.org/copter/docs/common-optical-flow-sensor-setup.html).

Most of the settings should already be inputted for the last 3 steps, but the exact tuning will be different for every drone.

8. To use Loiter mode without a GPS (uses optical flow and rangefinder), you need to "Set EKF home here" in Mission Planner by right clicking on the map. 



9. Happy Flying.

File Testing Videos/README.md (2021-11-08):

# Testing Videos

The tesing videos for this project can be found in the following playlist:
https://www.youtube.com/playlist?list=PLAno-y1b9fZaF9x1nrwcfBmPpxw2qFB2O

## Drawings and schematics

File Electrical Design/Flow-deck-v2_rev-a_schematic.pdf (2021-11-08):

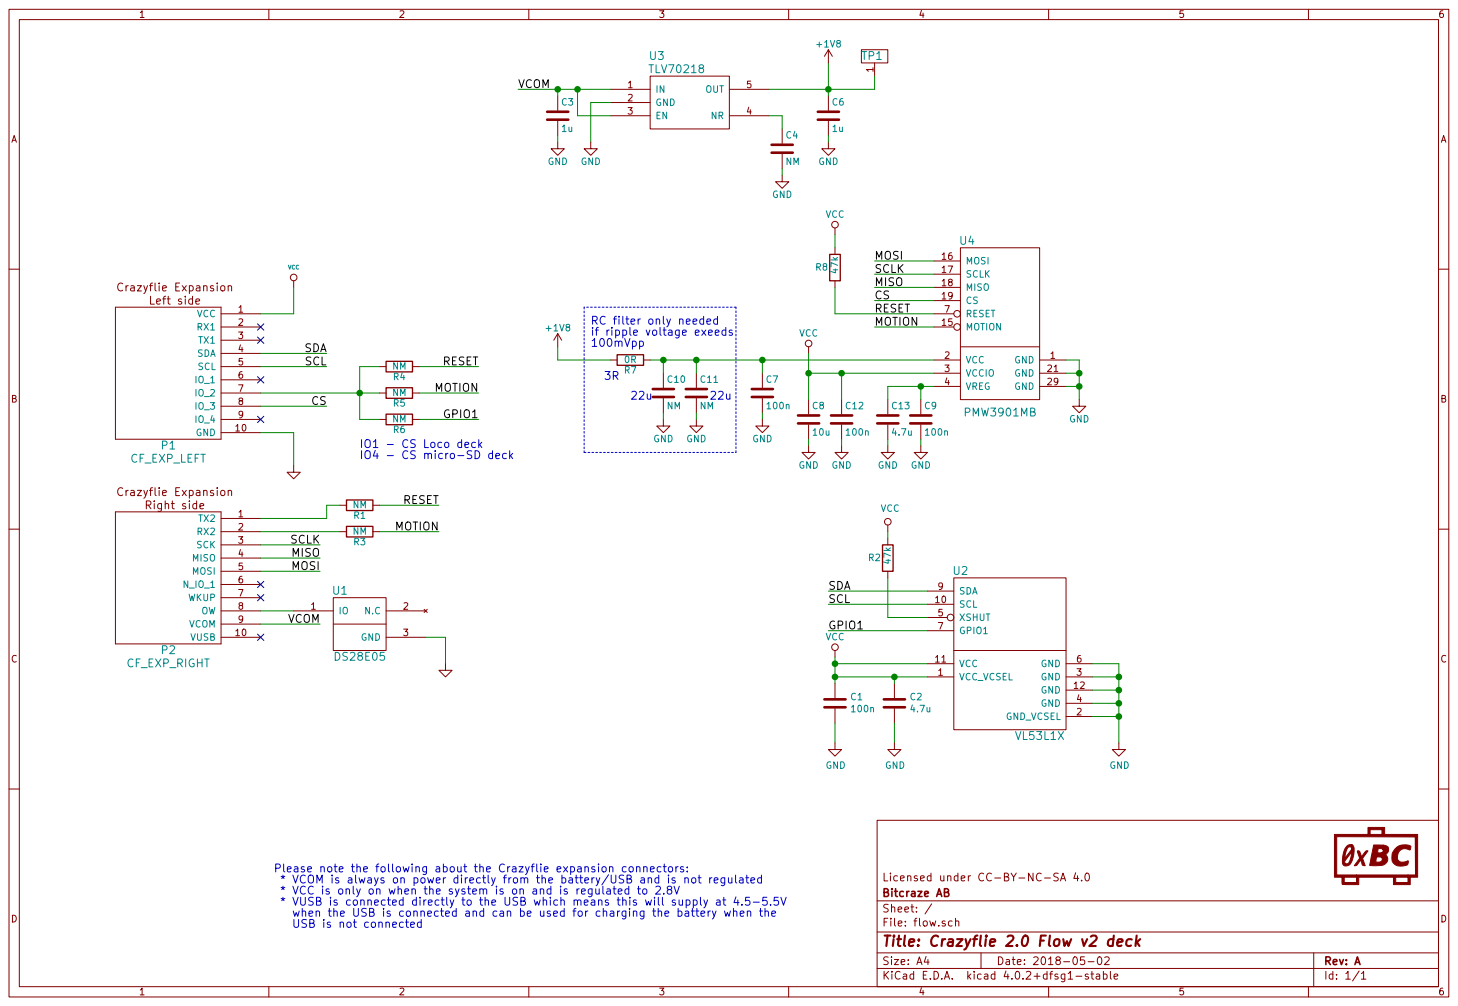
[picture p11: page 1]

R8 47k VCC RC filter only needed

if ripple voltage exeeds
100mVpp

IO1 - CS Loco deck
IO4 - CS micro-SD deck R1 NM

Please note the following about the Crazyflie expansion connectors:
* VCOM is always on power directly from the battery/USB and is not regulated
* VCC is only on when the system is on and is regulated to 2.8V
* VUSB is connected directly to the USB which means this will supply at 4.5-5.5V
when the USB is connected and can be used for charging the battery when the
USB is not connected

Licensed under CC-BY-NC-SA 4.0
File: flow.sch Sheet: / Bitcraze AB

Id: 1/1 Title: Crazyflie 2.0 Flow v2 deck

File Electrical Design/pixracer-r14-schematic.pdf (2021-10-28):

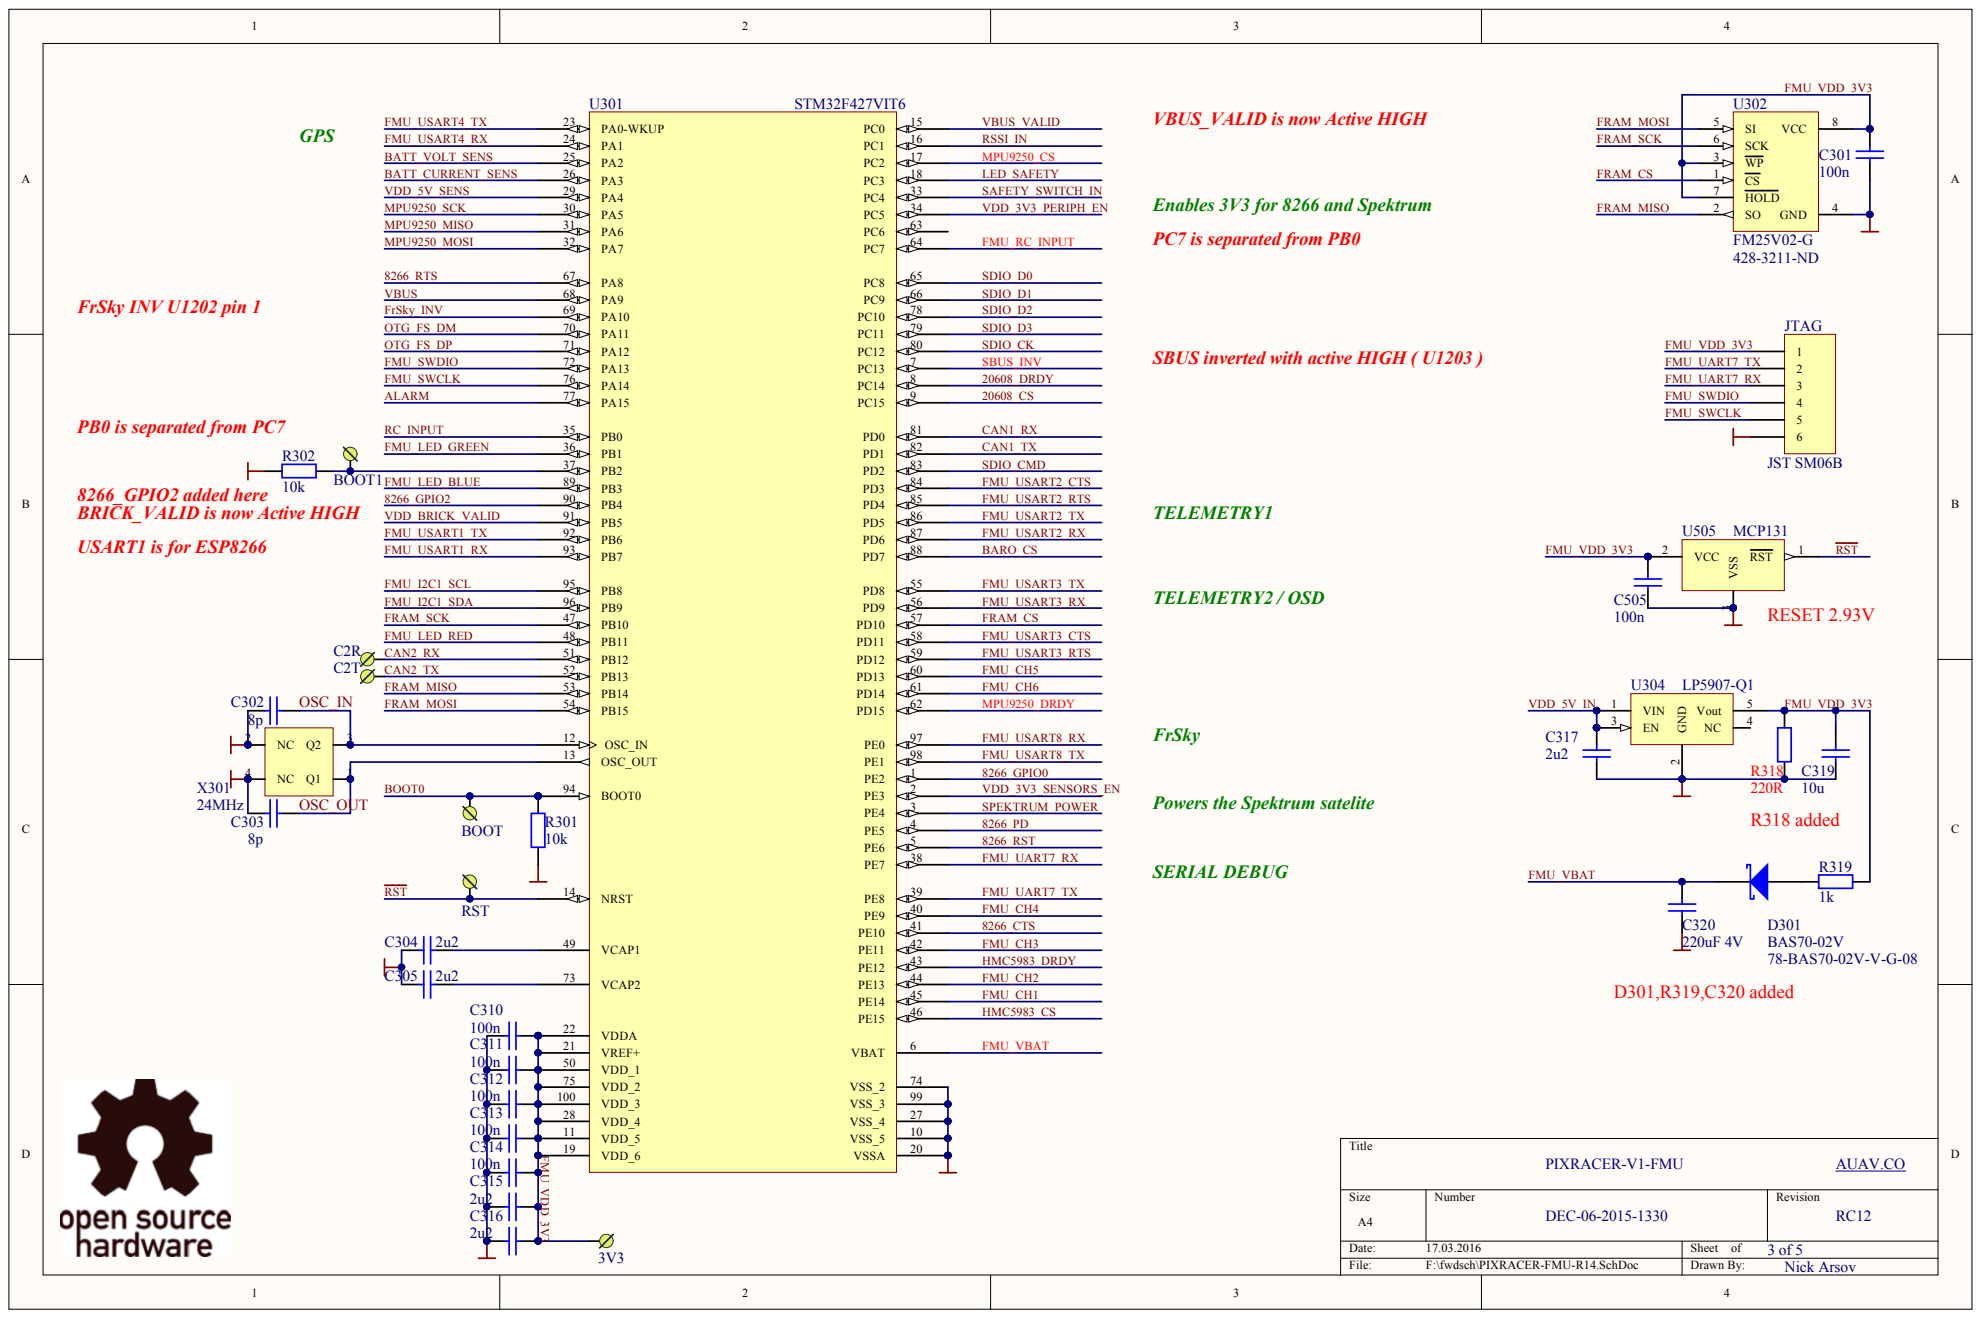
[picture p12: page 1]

Enables 3V3 for 8266 and Spektrum

PC7 is separated from PB

SBUS inverted with active HIGH ( U1203 )

PB0 is separated from PC

BRICK_VALID is now Active HIGH

Powers the Spektrum satelite

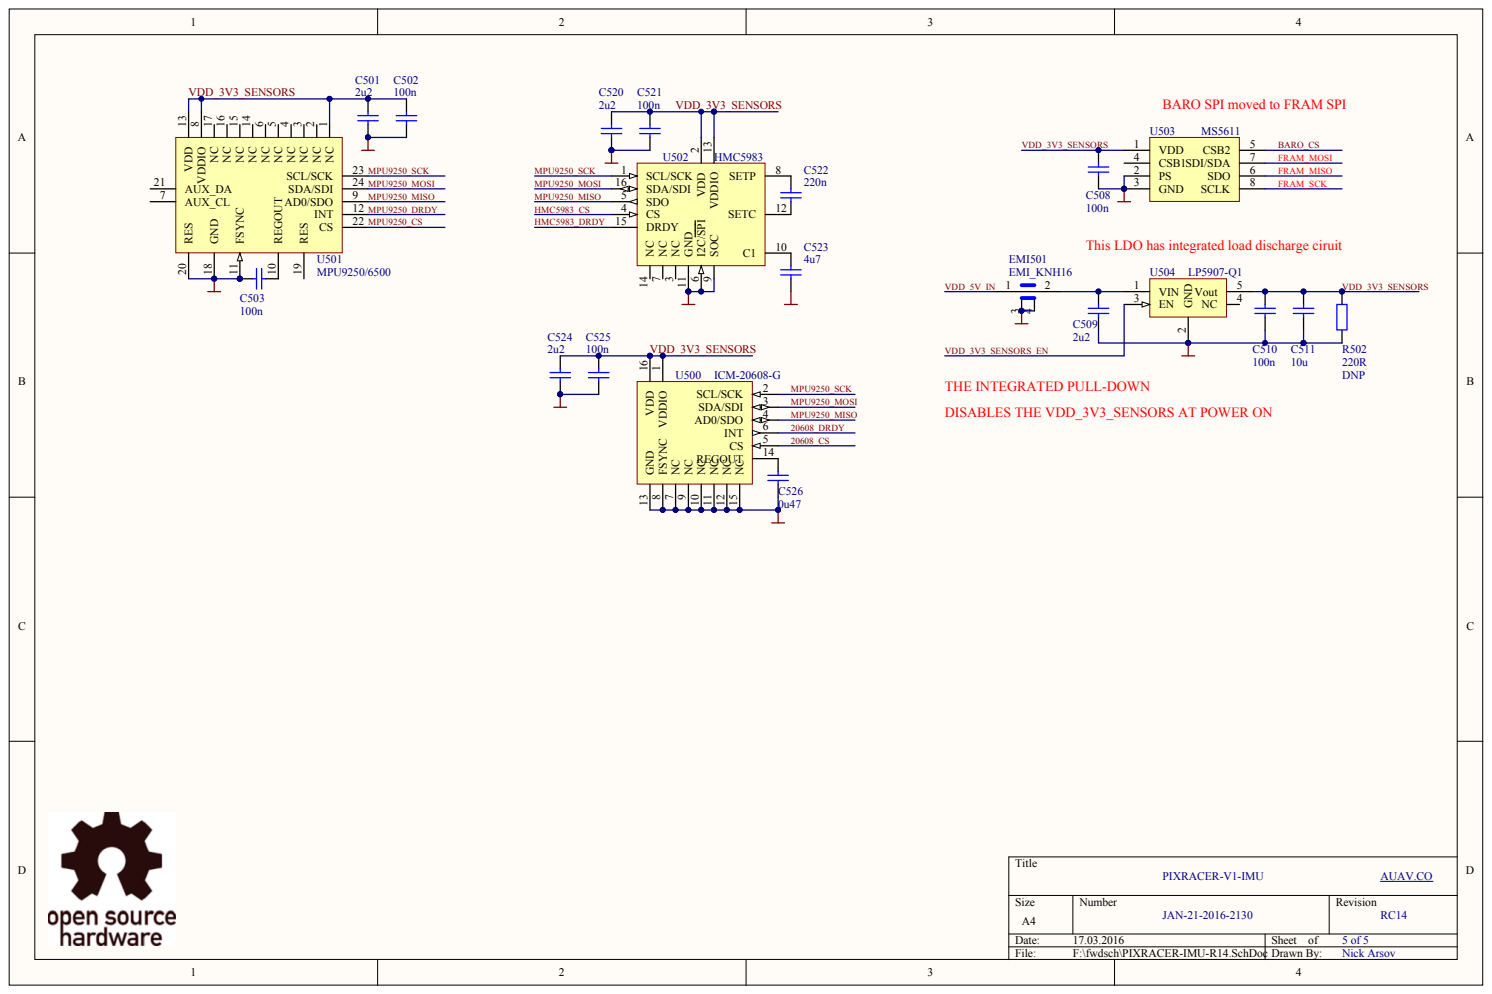
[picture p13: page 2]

BARO SPI moved to FRAM SPI

NC 14 NC 15 NC 16 NC 17 GND 18

This LDO has integrated load discharge ciruit

V D D_3V3_SEN S

THE INTEGRATED PULL-DOWN

DISABLES THE VDD_3V3_SENSORS AT POWER ON

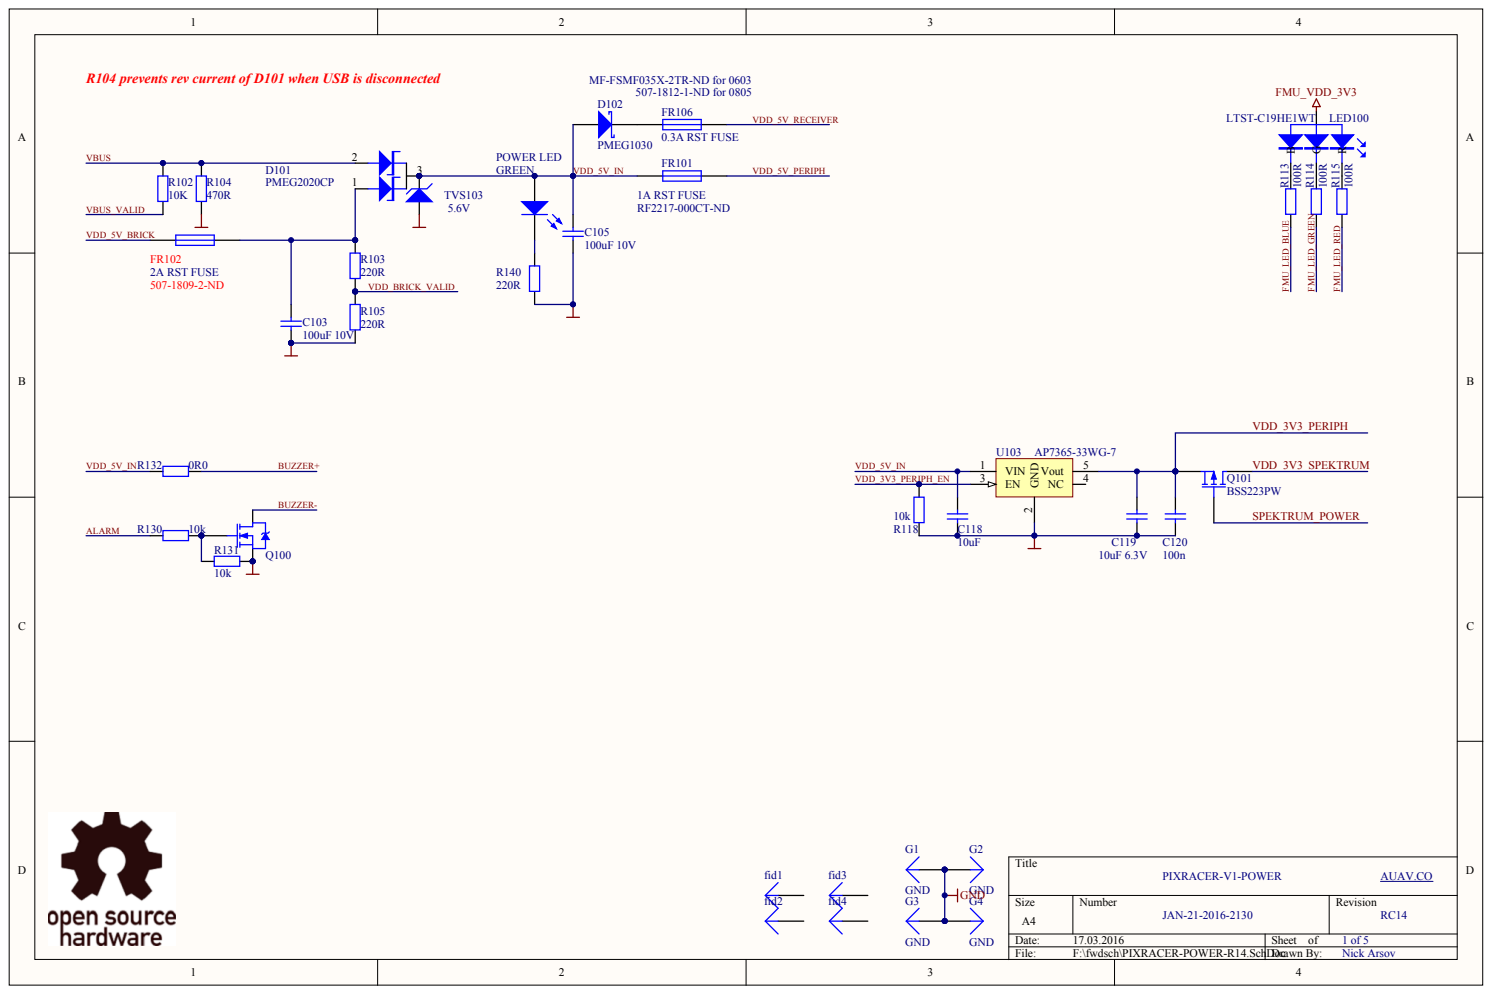
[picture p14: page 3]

R104 prevents rev current of D101 when USB is disconnected

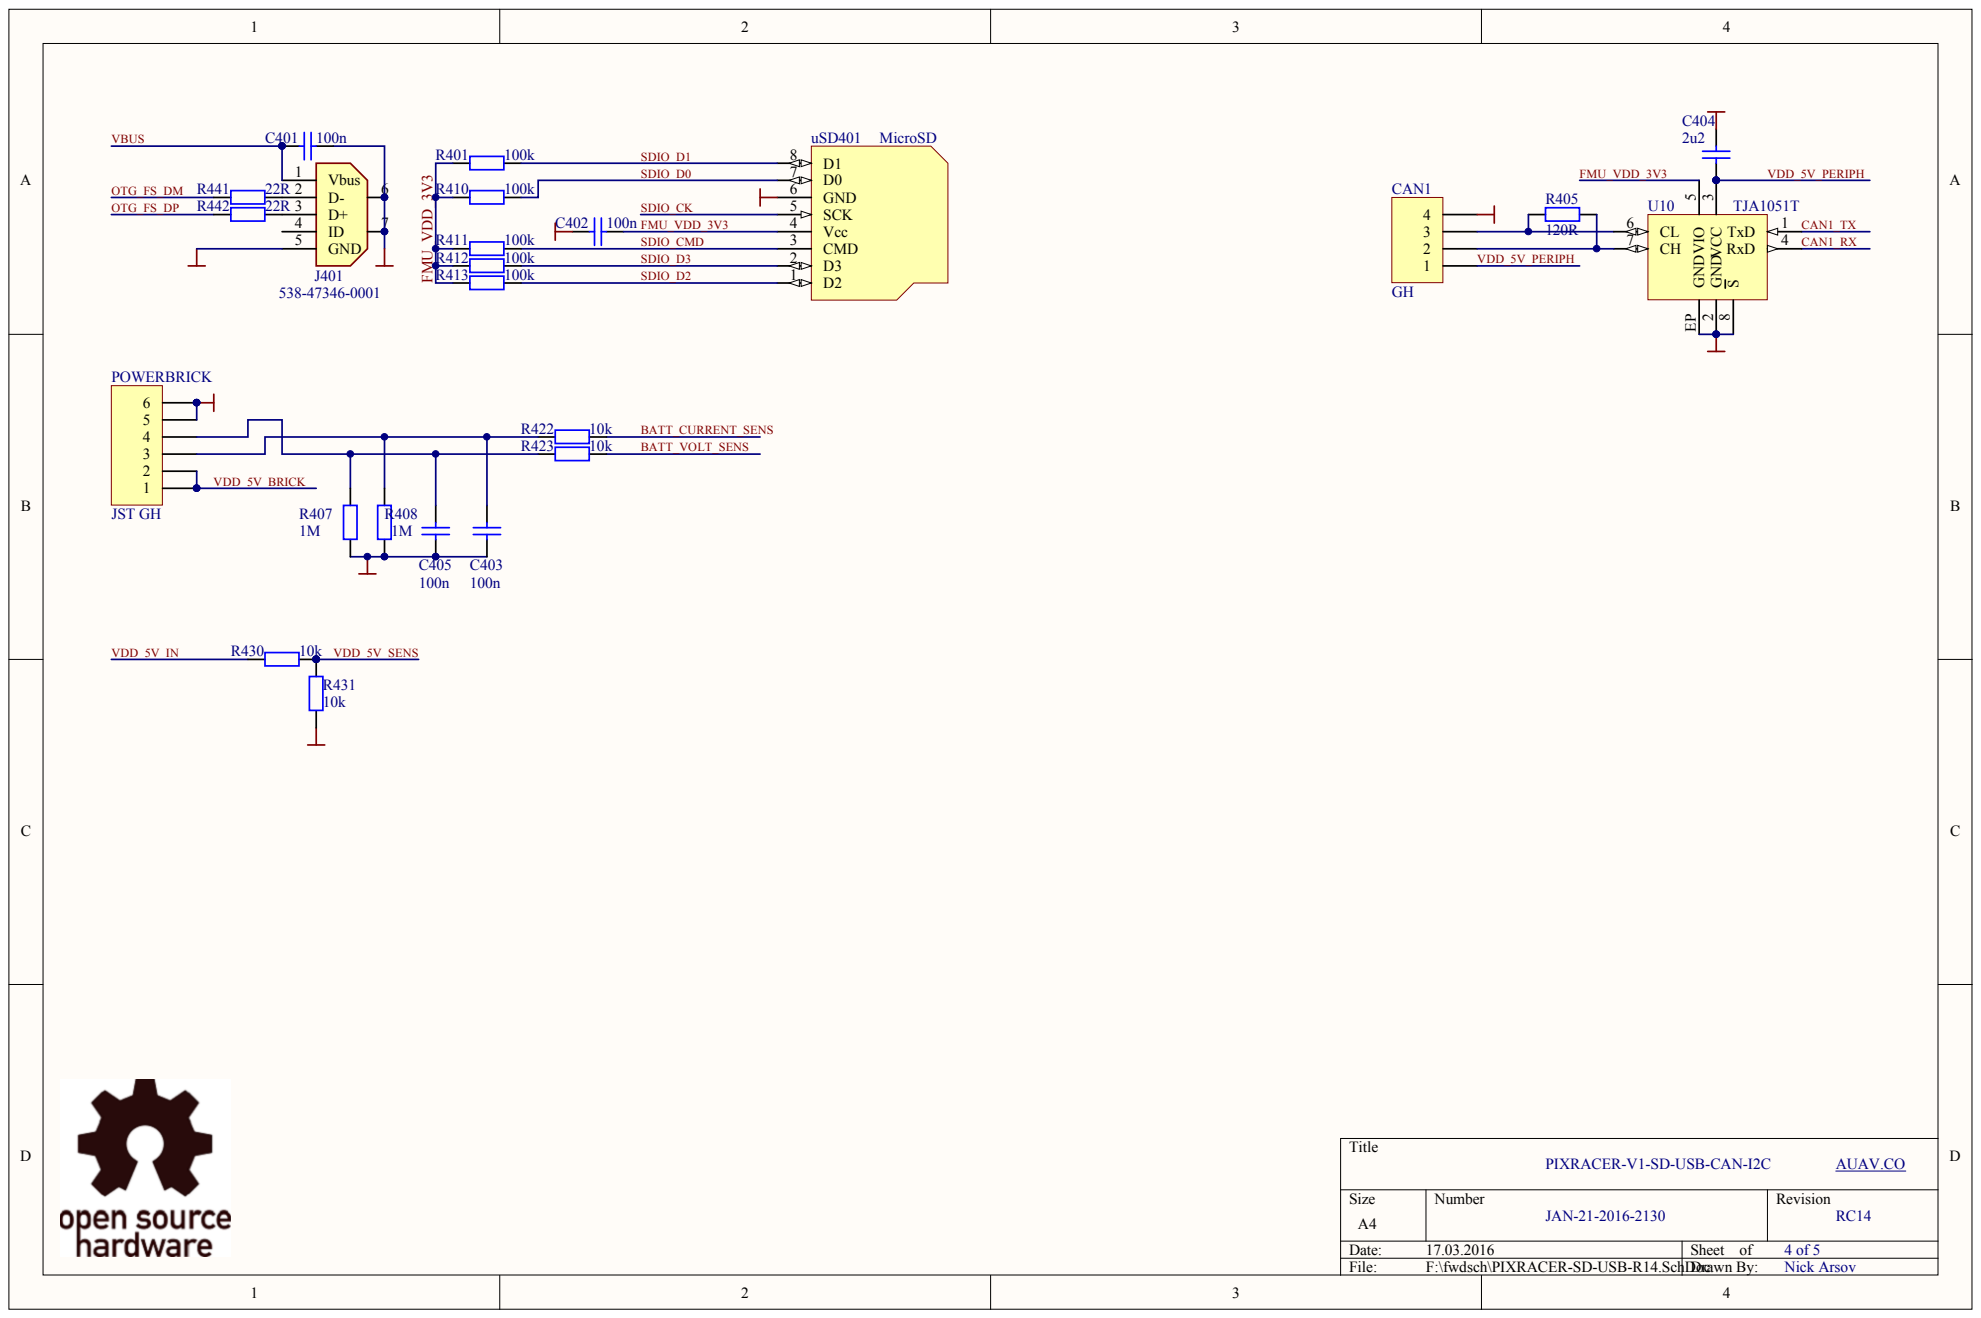
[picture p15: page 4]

PIXRACER-V1-SD-USB-CAN-I2C

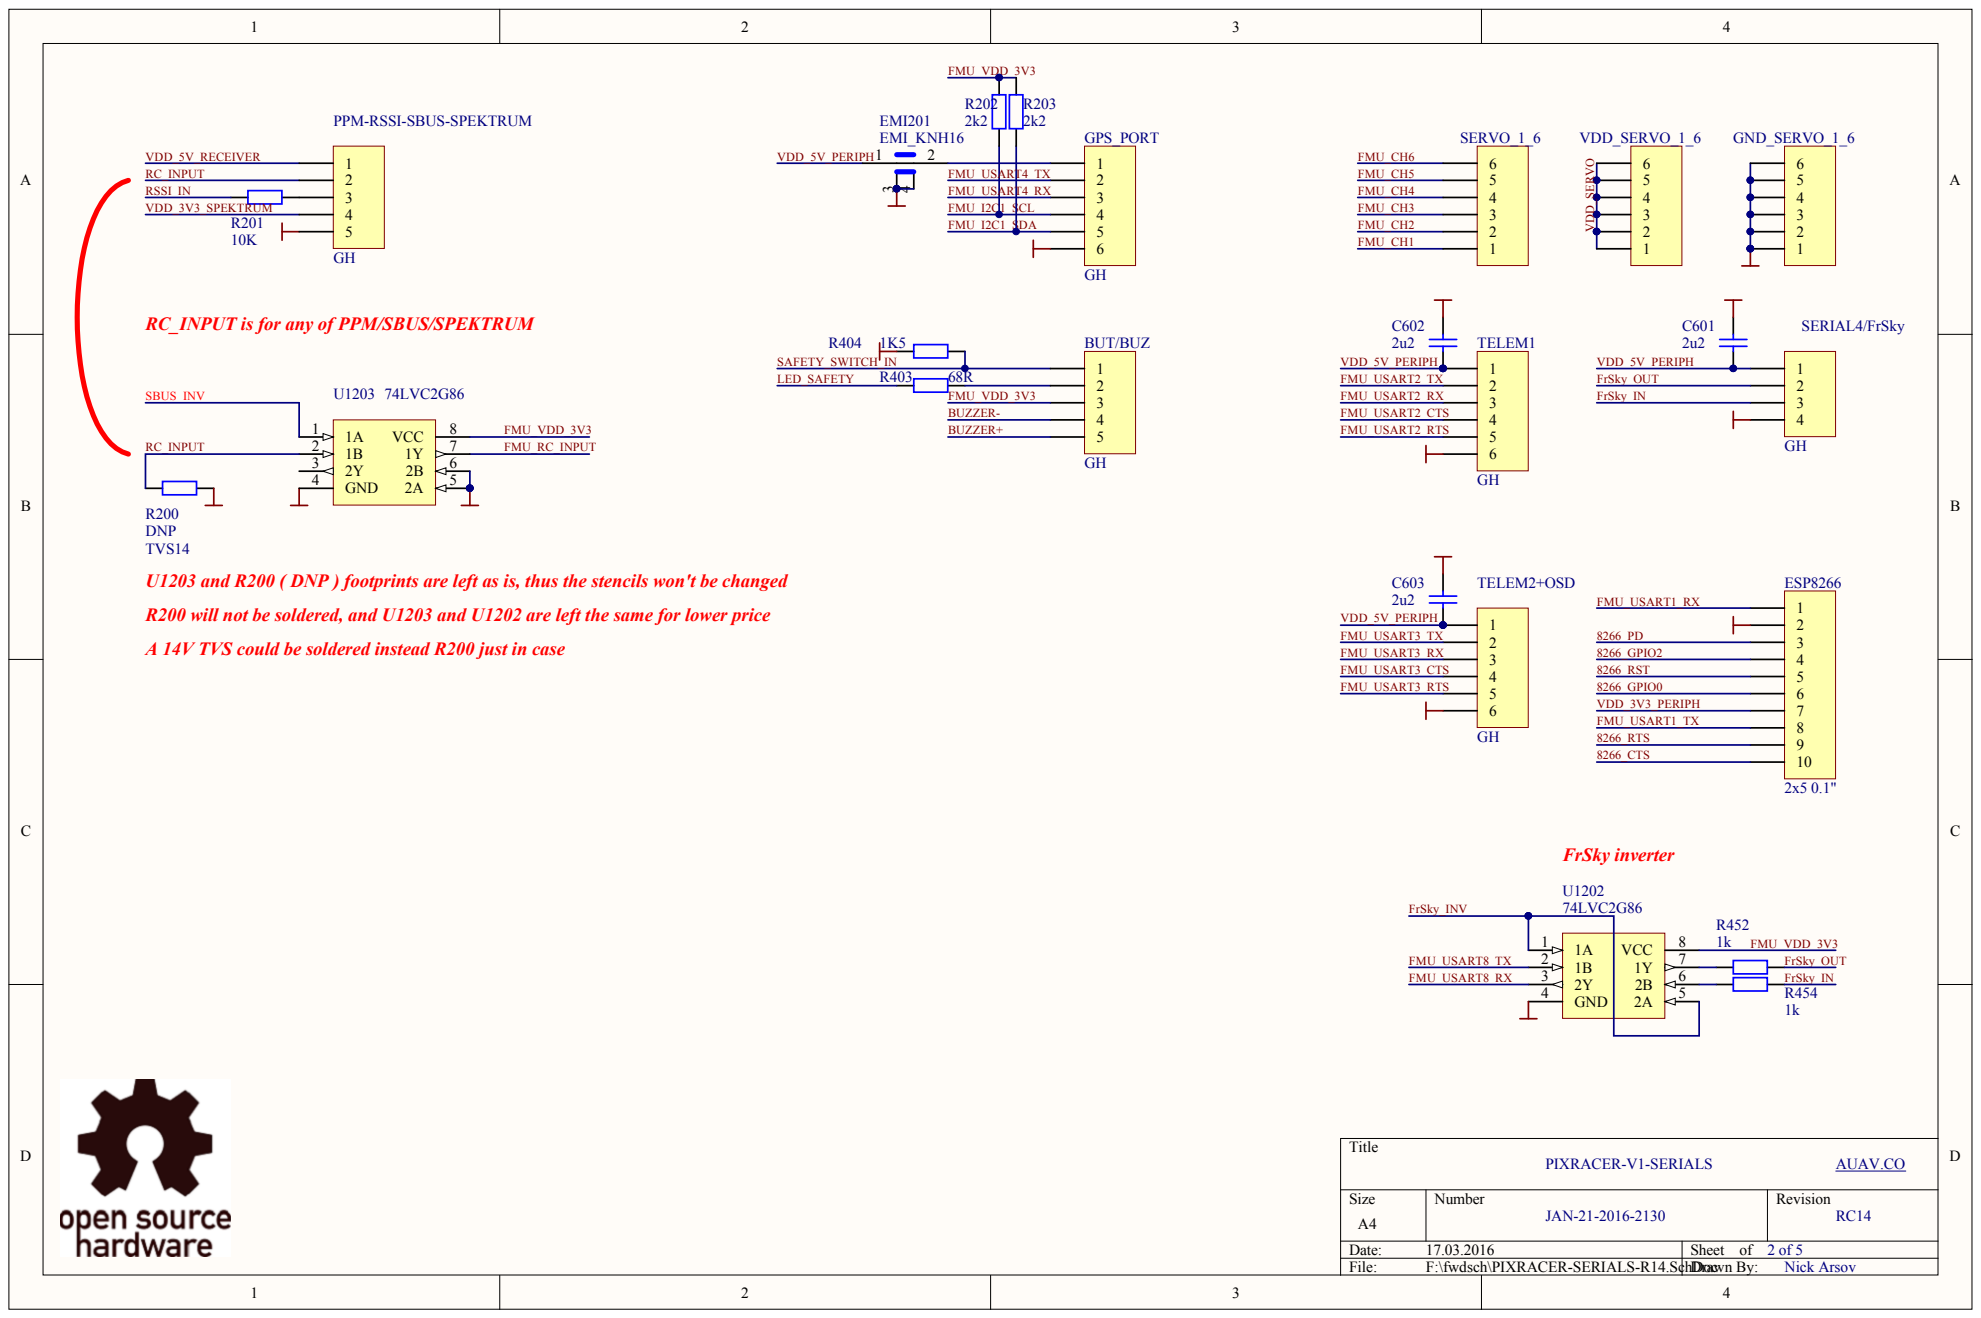
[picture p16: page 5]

PPM-RSSI-SBUS-SPEKTRUM

DNP
TVS14
U1203 and R200 ( DNP ) footprints are left as is, thus the stencils won't be changed

R200 will not be soldered, and U1203 and U1202 are left the same for lower price

A 14V TVS could be soldered instead R200 just in case

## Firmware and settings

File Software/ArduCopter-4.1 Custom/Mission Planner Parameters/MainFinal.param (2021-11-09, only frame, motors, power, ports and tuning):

ATC_ANG_LIM_TC,1
ATC_ANG_PIT_P,4.5
ATC_ANG_RLL_P,4.5
ATC_ANG_YAW_P,4.5
ATC_ANGLE_BOOST,1
ATC_RAT_PIT_D,0.0036
ATC_RAT_PIT_FF,0
ATC_RAT_PIT_FLTD,50
ATC_RAT_PIT_FLTE,0
ATC_RAT_PIT_FLTT,50
ATC_RAT_PIT_I,0.135
ATC_RAT_PIT_IMAX,0.5
ATC_RAT_PIT_P,0.135
ATC_RAT_PIT_SMAX,0
ATC_RAT_RLL_D,0.0036
ATC_RAT_RLL_FF,0
ATC_RAT_RLL_FLTD,50
ATC_RAT_RLL_FLTE,0
ATC_RAT_RLL_FLTT,50
ATC_RAT_RLL_I,0.135
ATC_RAT_RLL_IMAX,0.5
ATC_RAT_RLL_P,0.135
ATC_RAT_RLL_SMAX,0
ATC_RAT_YAW_D,0
ATC_RAT_YAW_FF,0
ATC_RAT_YAW_FLTD,0
ATC_RAT_YAW_FLTE,2
ATC_RAT_YAW_FLTT,50
ATC_RAT_YAW_I,0.018
ATC_RAT_YAW_IMAX,0.5
ATC_RAT_YAW_P,0.18
ATC_RAT_YAW_SMAX,0
ATC_RATE_FF_ENAB,1
ATC_RATE_P_MAX,0
ATC_RATE_R_MAX,0
ATC_RATE_Y_MAX,0
BATT_AMP_OFFSET,0
BATT_AMP_PERVLT,39.877
BATT_ARM_MAH,0
BATT_ARM_VOLT,0
BATT_BUS,0
BATT_CAPACITY,460
BATT_CRT_MAH,0
BATT_CRT_VOLT,0
BATT_CURR_PIN,3
BATT_FS_CRT_ACT,0
BATT_FS_LOW_ACT,0
BATT_FS_VOLTSRC,0
BATT_LOW_MAH,0
BATT_LOW_TIMER,10
BATT_LOW_VOLT,6
BATT_MONITOR,4
BATT_OPTIONS,0
BATT_SERIAL_NUM,-1
BATT_VOLT_MULT,12.24
BATT_VOLT_PIN,2
BATT2_MONITOR,0
BATT3_MONITOR,0
BATT4_MONITOR,0
BATT5_MONITOR,0
BATT6_MONITOR,0
BATT7_MONITOR,0
BATT8_MONITOR,0
BATT9_MONITOR,0
FLTMODE_CH,5
FLTMODE1,0
FLTMODE2,0
FLTMODE3,0
FLTMODE4,2
FLTMODE5,0
FLTMODE6,5
FRAME_CLASS,1
FRAME_TYPE,1
INS_GYRO_FILTER,100
INS_HNTCH_ENABLE,0
MOT_BAT_CURR_MAX,0
MOT_BAT_CURR_TC,5
MOT_BAT_IDX,0
MOT_BAT_VOLT_MAX,8.4
MOT_BAT_VOLT_MIN,6.6
MOT_BOOST_SCALE,0
MOT_HOVER_LEARN,2
MOT_PWM_MAX,0
MOT_PWM_MIN,0
MOT_PWM_TYPE,5
MOT_SAFE_DISARM,0
MOT_SAFE_TIME,1
MOT_SLEW_DN_TIME,0
MOT_SLEW_UP_TIME,0
MOT_SPIN_ARM,0.1
MOT_SPIN_MAX,0.95
MOT_SPIN_MIN,0.15
MOT_SPOOL_TIME,0.5
MOT_THST_EXPO,0.5
MOT_THST_HOVER,0.2713512
MOT_YAW_HEADROOM,200
SERIAL0_BAUD,115
SERIAL0_PROTOCOL,2
SERIAL1_BAUD,921
SERIAL1_OPTIONS,0
SERIAL1_PROTOCOL,2
SERIAL2_BAUD,921
SERIAL2_OPTIONS,0
SERIAL2_PROTOCOL,2
SERIAL3_BAUD,38
SERIAL3_OPTIONS,0
SERIAL3_PROTOCOL,5
SERIAL4_BAUD,38
SERIAL4_OPTIONS,0
SERIAL4_PROTOCOL,5
SERIAL5_BAUD,921600
SERIAL5_OPTIONS,0
SERIAL5_PROTOCOL,1
SERIAL6_BAUD,57
SERIAL6_OPTIONS,0
SERIAL6_PROTOCOL,-1
SERVO1_FUNCTION,33
SERVO1_MAX,1900
SERVO1_MIN,1100
SERVO1_REVERSED,0
SERVO1_TRIM,1500
SERVO2_FUNCTION,36
SERVO2_MAX,1900
SERVO2_MIN,1100
SERVO2_REVERSED,0
SERVO2_TRIM,1500
SERVO3_FUNCTION,35
SERVO3_MAX,1900
SERVO3_MIN,1100
SERVO3_REVERSED,0
SERVO3_TRIM,1500
SERVO4_FUNCTION,34
SERVO4_MAX,1900
SERVO4_MIN,1100
SERVO4_REVERSED,0
SERVO4_TRIM,1500
SERVO5_FUNCTION,0
SERVO5_MAX,1900
SERVO5_MIN,1100
SERVO5_REVERSED,0
SERVO5_TRIM,1500
SERVO6_FUNCTION,0
SERVO6_MAX,1900
SERVO6_MIN,1100
SERVO6_REVERSED,0
SERVO6_TRIM,1500
SERVO7_FUNCTION,0
SERVO7_MAX,1900
SERVO7_MIN,1100
SERVO7_REVERSED,0
SERVO7_TRIM,1500
SERVO8_FUNCTION,0
SERVO8_MAX,1900
SERVO8_MIN,1100
SERVO8_REVERSED,0
SERVO8_TRIM,1500
SERVO9_FUNCTION,0
SERVO9_MAX,1900
SERVO9_MIN,1100
SERVO9_REVERSED,0
SERVO9_TRIM,1500

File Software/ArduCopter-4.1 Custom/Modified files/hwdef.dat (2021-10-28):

# hw definition file for processing by chibios_hwdef.py for the
# mRo Pixracer board. This is a fmuv4 board

define CONFIG_HAL_BOARD_SUBTYPE HAL_BOARD_SUBTYPE_CHIBIOS_FMUV4

# MCU class and specific type
MCU STM32F4xx STM32F427xx

# board ID for firmware load
APJ_BOARD_ID 11

# crystal frequency
OSCILLATOR_HZ 24000000


# ChibiOS system timer
STM32_ST_USE_TIMER 5

# flash size
FLASH_SIZE_KB 2048

env OPTIMIZE -O2

# serial port for stdout disabled, use USB console
# STDOUT_SERIAL SD7
# STDOUT_BAUDRATE 57600

# only one I2C bus
I2C_ORDER I2C1

# to match px4 we make the first bus number 1
define HAL_I2C_BUS_BASE 1
define HAL_I2C_INTERNAL_MASK 0

# order of UARTs (and USB)
SERIAL_ORDER OTG1 USART2 USART3 UART4 UART8 USART1 UART7

# UART4 is GPS
PA0 UART4_TX UART4
PA1 UART4_RX UART4
PA2 BATT_VOLTAGE_SENS ADC1
PA3 BATT_CURRENT_SENS ADC1
PA4 VDD_5V_SENS ADC1 SCALE(2)

# SPI1 is sensors bus
PA5 SPI1_SCK SPI1
PA6 SPI1_MISO SPI1
PA7 SPI1_MOSI SPI1

PA9 VBUS INPUT

PA11 OTG_FS_DM OTG1
PA12 OTG_FS_DP OTG1

PA13 JTMS-SWDIO SWD
PA14 JTCK-SWCLK SWD

# PWM output for buzzer
PA15 TIM2_CH1 TIM2 GPIO(77) ALARM

# control of spektrum power pin
PE4 SPEKTRUM_PWR OUTPUT LOW GPIO(70)
define HAL_GPIO_SPEKTRUM_PWR 70

# spektrum power is active low
define HAL_SPEKTRUM_PWR_ENABLED 0

# spektrum RC input pin, used as GPIO for bind for satellite receivers
PB0 SPEKTRUM_RC INPUT PULLUP GPIO(71)
define HAL_GPIO_SPEKTRUM_RC 71

PB2 BOOT1 INPUT
PB5 VDD_BRICK_VALID INPUT PULLDOWN

# USART1 is disabled (was ESP8266)
PB6 USART1_TX USART1
PB7 USART1_RX USART1
PA8 USART1_RTS USART1
# PE10 is not a hw CTS pin for USART1
PE10 8266_CTS INPUT

# old (make GPIOs for ESP8266 available via mavlink relay control as pins)
# 60 to 63
# comment out these four lines to enable SPI
#PB4 8266_GPIO2 OUTPUT GPIO(60)
#PE2 8266_GPI0 INPUT PULLUP GPIO(61)
#PE5 8266_PD OUTPUT HIGH GPIO(62)
#PE6 8266_RST OUTPUT HIGH GPIO(63)

# Setup the SPI4 GPIO's for flowdeck v2 (just the PMW3901 optical flow sensor)
# Uncomment these 4 lines and the lines further below to enable pixartflow
PB4 FLOW_CS CS
PE2 SPI4_SCK SPI4
PE5 SPI4_MISO SPI4
PE6 SPI4_MOSI SPI4

# I2C for flowdeck v2 (just the VL53L1x range finder)
PB8 I2C1_SCL I2C1
PB9 I2C1_SDA I2C1

# SPI2 is FRAM
PB10 SPI2_SCK SPI2
PB12 CAN2_RX CAN2
PB13 CAN2_TX CAN2 # this is SPI2_SCK on beta board
PB14 SPI2_MISO SPI2
PB15 SPI2_MOSI SPI2

PC0 VBUS_VALID INPUT PULLDOWN
PC1 RSSI_IN ADC1
PC2 MPU9250_CS CS
PC3 LED_SAFETY OUTPUT
PC4 SAFETY_IN INPUT PULLDOWN
PC5 VDD_PERIPH_EN OUTPUT HIGH

PC7 TIM8_CH2 TIM8 RCININT FLOAT LOW # also USART6_RX for serial RC
PC13 SBUS_INV OUTPUT LOW

PC8 SDIO_D0 SDIO
PC9 SDIO_D1 SDIO
PC10 SDIO_D2 SDIO
PC11 SDIO_D3 SDIO
PC12 SDIO_CK SDIO


PC14 20608_DRDY INPUT
PC15 20608_CS CS

PD0 CAN1_RX CAN1
PD1 CAN1_TX CAN1
PD2 SDIO_CMD SDIO

# USART2 serial2 telem1
PD3 USART2_CTS USART2
PD4 USART2_RTS USART2
PD5 USART2_TX USART2
PD6 USART2_RX USART2

PD7 BARO_CS CS

# USART3 serial3 telem2
PD8 USART3_TX USART3
PD9 USART3_RX USART3
PD10 FRAM_CS CS
PD11 USART3_CTS USART3
PD12 USART3_RTS USART3

PD15 MPU9250_DRDY INPUT

# UART8 serial4 FrSky
PE0 UART8_RX UART8
PE1 UART8_TX UART8

# allow this uart to be inverted for transmit under user control
# the polarity is the value to use on the GPIO to change the polarity
# to the opposite of the default
PA10 UART8_TXINV OUTPUT HIGH GPIO(78) POL(0)

PE3 VDD_SENSORS_EN OUTPUT HIGH

# UART7 is debug
PE7 UART7_RX UART7 NODMA
PE8 UART7_TX UART7 NODMA

PE14 TIM1_CH4 TIM1 PWM(1) GPIO(50)
PE13 TIM1_CH3 TIM1 PWM(2) GPIO(51)
PE11 TIM1_CH2 TIM1 PWM(3) GPIO(52)
PE9  TIM1_CH1 TIM1 PWM(4) GPIO(53)
PD13 TIM4_CH2 TIM4 PWM(5) GPIO(54)
PD14 TIM4_CH3 TIM4 PWM(6) GPIO(55)

PE12 MAG_DRDY INPUT
PE15 MAG_CS CS

# SPI device table. The DEVID values are chosen to match the PX4 port
# of ArduPilot so users don't need to re-do their accel and compass calibrations
# when moving to ChibiOS
SPIDEV ms5611_int  SPI2 DEVID3  BARO_CS    MODE3  20*MHZ  20*MHZ
SPIDEV mpu9250     SPI1 DEVID4  MPU9250_CS MODE3   2*MHZ   4*MHZ
SPIDEV icm20608    SPI1 DEVID6  20608_CS   MODE3   2*MHZ   8*MHZ
SPIDEV hmc5843     SPI1 DEVID5  MAG_CS     MODE3  11*MHZ  11*MHZ
SPIDEV lis3mdl     SPI1 DEVID5  MAG_CS     MODE3 500*KHZ 500*KHZ
SPIDEV ramtron     SPI2 DEVID10 FRAM_CS    MODE3   8*MHZ   8*MHZ
# Enable pixartflow
SPIDEV pixartflow  SPI4 DEVID2  FLOW_CS    MODE3   2*MHZ   2*MHZ

define HAL_CHIBIOS_ARCH_FMUV4 1

define HAL_BOARD_LOG_DIRECTORY "/APM/LOGS"
define HAL_BOARD_TERRAIN_DIRECTORY "/APM/TERRAIN"

define HAL_STORAGE_SIZE        16384

# enable RAMTROM parameter storage
define HAL_WITH_RAMTRON 1

# enable FAT filesystem
define HAL_OS_FATFS_IO 1

# pixracer has 3 LEDs, Red, Green, Blue
define HAL_HAVE_PIXRACER_LED

define HAL_GPIO_LED_ON  0
define HAL_GPIO_LED_OFF 1

# LED setup for PixracerLED driver
PB11 LED_RED   OUTPUT GPIO(0)
PB1  LED_GREEN OUTPUT GPIO(1)
PB3  LED_BLUE  OUTPUT GPIO(2)

define HAL_GPIO_A_LED_PIN 0
define HAL_GPIO_B_LED_PIN 1
define HAL_GPIO_C_LED_PIN 2

# battery setup
define HAL_BATT_VOLT_PIN 2
define HAL_BATT_CURR_PIN 3
define HAL_BATT_VOLT_SCALE 10.1
define HAL_BATT_CURR_SCALE 17.0

# setup serial port defaults for ESP8266
define HAL_SERIAL5_PROTOCOL SerialProtocol_MAVLink2
define HAL_SERIAL5_BAUD 921600

# 6 PWM available by default
define BOARD_PWM_COUNT_DEFAULT 6

# Define pixartflow
define HAL_HAVE_PIXARTFLOW_SPI

# two IMUs
IMU Invensense SPI:icm20608 ROTATION_ROLL_180_YAW_90
IMU Invensense SPI:mpu9250 ROTATION_ROLL_180_YAW_90
define HAL_DEFAULT_INS_FAST_SAMPLE 1

# 2 compasses. R15 has LIS3MDL instead of HMC5843
COMPASS HMC5843 SPI:hmc5843 false ROTATION_PITCH_180
COMPASS LIS3MDL SPI:lis3mdl false ROTATION_NONE
COMPASS AK8963:probe_mpu9250 0 ROTATION_ROLL_180_YAW_90

# also probe all types of external I2C compasses
define HAL_PROBE_EXTERNAL_I2C_COMPASSES

# one barometer
BARO MS56XX SPI:ms5611_int

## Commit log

2021-07-22 Basic file structure setup
    [Component list.xlsx]
2021-07-26 excel update
    [Component list.xlsx]
2021-10-28 28th of the 10th 2021
    [11 42 on the 20 of the 10.param, 25 of 10th 9 27.param, Component list.xlsx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]
2021-10-28 add instructions
    [BOM.xlsx]
2021-11-08 08/11 8:24
    [65mm Press-Fit Prop v1.f3d, ESP-01S (ESP8266) Board Module v1.f3d, Frame 1.f3z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]
2021-11-08 08/11 test
    [Frame_carriage.stl]
2021-11-09 fix bom
    [BOM.xlsx]
